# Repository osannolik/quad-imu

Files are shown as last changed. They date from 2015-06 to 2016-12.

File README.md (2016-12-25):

Quadcopter or general 6 DOF IMU
===========================

## Hardware

* ARM Cortex-M4, STM32F405, 168 MHz, FPU
* Accelerometer and gyro ICM20608
* 2.4 GHz Transceiver nRF24L01+
* USB Power Manager with Li-Ion charger LTC3553
* USB to serial UART interface FT232RQ 

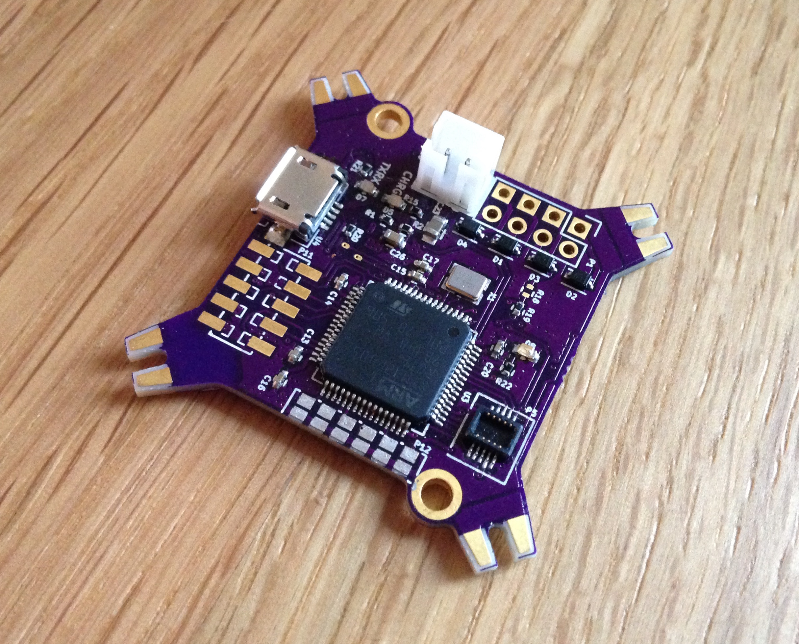
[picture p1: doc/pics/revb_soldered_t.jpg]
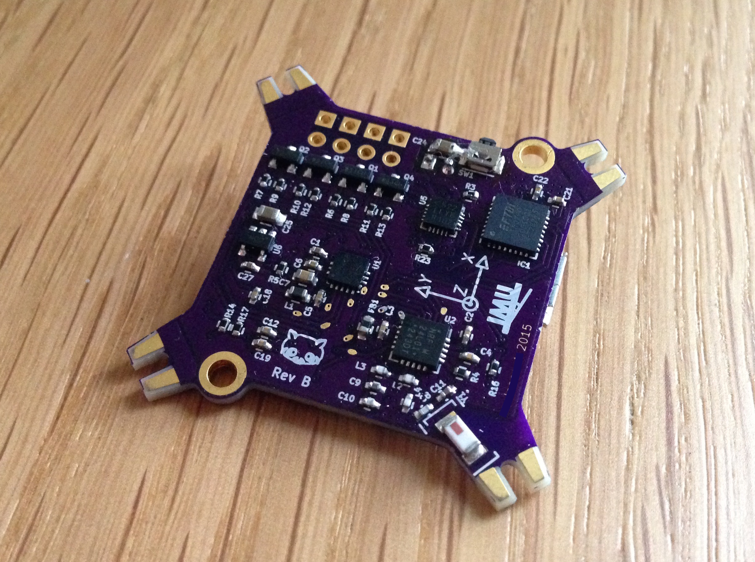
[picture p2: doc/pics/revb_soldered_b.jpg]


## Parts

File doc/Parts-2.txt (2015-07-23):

FT232R (dk 768-1008-1-ND)
USB B micro (dk 609-4052-1-ND)
Switch (dk SW1022CT-ND)

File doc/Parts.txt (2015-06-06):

//MPU-9250
ICM-20608 (dk 1428-1052-1-ND)
STM32F405RGT6 (dk 497-11767-ND)
nRF24L01P
LTC3553 (dk LTC3553EUD#PBF-ND)
//LTC4063 (dk LTC4063EDD#PBF-ND)
LED 0603 (dk 475-2512-1-ND)
//LP2992 LDO (dk LP2992AIM5-3.3/NOPBCT-ND)
TLV70033 LDO (dk 296-27937-1-ND)
Ferrite 0603 600ohm @ 100MHz (dk MH1608-601YCT-ND)
Inductor 0603 2.2uH (dk 445-3164-1-ND)
Chip antenna (dk 712-1005-1-ND)
BAT54WS SOD-323 (dk BAT54WS-TPCT-ND)
ST-Link v2 (dk 497-10484-ND)
ST-Link JTAG 20-10 pin converter (dk 1188-1016-ND)
Debug connector (dk H121938CT-ND) på kort
Debug connector (dk H124689CT-ND) på adapter
Crystal (dk SER3628CT-ND)
Caps 100nF 0402 (dk 1276-1001-1-ND)
Caps 470nF 0402 (dk 445-4996-1-ND)
Caps 33nF 0402 (dk 1276-1177-1-ND)
Caps 10nF 0402 (dk 1276-1051-1-ND)
Caps 1nF 0402 (dk 1276-1032-1-ND)
Caps 4.7uF 0603 (dk 1276-2087-1-ND)
Caps 2.2uF 0402 (dk 1276-1469-1-ND)
Caps 1uF 0402 (dk 1276-1444-1-ND)
Caps 10uF 0805 (dk 1276-2402-1-ND)
Caps 22uF 0805 (dk 1276-2412-1-ND)

Header female 2mm 2x5 (dk H10963-ND)
USB B micro (dk 609-4052-1-ND)
Resistors 0402 ...

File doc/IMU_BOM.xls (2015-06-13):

Reference | Quantity | Value | Footprint | Digikey | Buy qty
C1 | 1 | 470n | Capacitors_SMD:C_0402 | 445-4996-1-ND | 10
C10 | 1 | 4p7 | Capacitors_SMD:C_0402 |  | 0
C11 | 1 | 1p | Capacitors_SMD:C_0402 |  | 0
C12 C13 | 2 | 2u2 | Capacitors_SMD:C_0402 | 1276-1469-1-ND | 10
C17 C27 | 2 | 1u | Capacitors_SMD:C_0402 | 1276-1444-1-ND | 10
C2 | 1 | 33n | Capacitors_SMD:C_0402 | 1276-1177-1-ND | 10
C23 C25 | 2 | 10u | Capacitors_SMD:C_0805 | 1276-2402-1-ND | 10
C24 | 1 | 22u | Capacitors_SMD:C_0805 | 1276-2412-1-ND | 10
C15 C3 | 2 | 10n | Capacitors_SMD:C_0402 | 1276-1051-1-ND | 100
C4 | 1 | 1n | Capacitors_SMD:C_0402 | 1276-1032-1-ND | 100
C14 C16 C18 C19 C20 C21 C22 C5 C6 | 9 | 100n | Capacitors_SMD:C_0402 | 1276-1001-1-ND | 100
C26 C7 | 2 | 4u7 | Capacitors_SMD:C_0603 | 1276-2087-1-ND | 10
C8 | 1 | 1p5 | Capacitors_SMD:C_0402 |  | 0
C9 | 1 | 2n2 | Capacitors_SMD:C_0402 |  | 0
D1 D2 D3 D4 | 4 | BAT54WS | Diodes_SMD:SOD-323 | BAT54WS-TPCT-ND | 10
D6 | 1 | TXLED | LEDs:LED-0603 | 754-1121-1-ND | 10
D7 | 1 | RXLED | LEDs:LED-0603 |  | 0
D5 D8 | 2 | LED | LEDs:LED-0603 | 475-2512-1-ND | 10
FB1 | 1 | 600R@100MHz | Capacitors_SMD:C_0603 | MH1608-601YCT-ND | 10
IC1 | 1 | FT232RQ | Housings_DFN_QFN:QFN-32-1EP_5x5mm_Pitch0.5mm |  | 0
L1 | 1 | 2u2 | Capacitors_SMD:C_0603 | 445-3164-1-ND | 5
L2 | 1 | 8n2 | Capacitors_SMD:C_0402 |  | 0
L3 | 1 | 2n7 | Capacitors_SMD:C_0402 |  | 0
L4 | 1 | 3n9 | Capacitors_SMD:C_0402 |  | 0
P1 | 1 | M1P | Wire_Pads:SolderWirePad_single_0-8mmDrill
P10 | 1 | CONN_01X02 | w_conn_jst-ph:b2b-ph-kl |  | 0
P11 | 1 | CONN_02X05 | molexNoHole:molexNoHole-87832-10 | H10963-ND | 2
P12 | 1 | CONN_02X06 | Connect:GS_6x2
P2 | 1 | M1N | Wire_Pads:SolderWirePad_single_0-8mmDrill
P3 | 1 | M3P | Wire_Pads:SolderWirePad_single_0-8mmDrill
P4 | 1 | M3N | Wire_Pads:SolderWirePad_single_0-8mmDrill
P5 | 1 | JTAG_DB | DF23C-10DP-0.5V:DF23C-10DP-0.5V | H121938CT-ND | 4
P6 | 1 | M2P | Wire_Pads:SolderWirePad_single_0-8mmDrill
P7 | 1 | M2N | Wire_Pads:SolderWirePad_single_0-8mmDrill
P8 | 1 | M4P | Wire_Pads:SolderWirePad_single_0-8mmDrill
P9 | 1 | M4N | Wire_Pads:SolderWirePad_single_0-8mmDrill
Q1 Q2 Q3 Q4 | 4 | IRFML8244 | Housings_SOT-23_SOT-143_TSOT-6:SOT-23 |  | 0
R1 | 1 | 560k | Resistors_SMD:R_0402 | 541-560KLCT-ND | 10
R10 R11 R14 R16 R17 R6 R7 | 7 | 100 | Resistors_SMD:R_0402 | 541-100JCT-ND | 20
R12 R13 R5 R8 R9 | 5 | 10k | Resistors_SMD:R_0402 | 541-10KJCT-ND | 20
R18 R19 | 2 | 100k | Resistors_SMD:R_0402 | 541-100KJCT-ND | 10
R2 | 1 | 180k | Resistors_SMD:R_0402 | 541-180KLCT-ND | 10
R15 R20 R21 R22 | 4 | 2k2 | Resistors_SMD:R_0402 | 541-2.2KJCT-ND | 10
R3 | 1 | 3k6 | Resistors_SMD:R_0402 | 541-3.6KJCT-ND | 10
R4 | 1 | 22k | Resistors_SMD:R_0402 | 541-22KJCT-ND | 10
U1 | 1 | ICM20608 | LGA16:LGA16 | 1428-1052-1-ND | 1
U2 | 1 | NRF24L01 | Housings_DFN_QFN:QFN-20-1EP_4x4mm_Pitch0.5mm |  | 0
U3 | 1 | STM32F405 | Housings_QFP:LQFP-64_10x10mm_Pitch0.5mm | 497-11767-ND | 1
U4 | 1 | MICRO-B_USB | USB-B-Micro:USB-B-Micro | 609-4052-1-ND | 1
U5 | 1 | LTC3553 | Housings_DFN_QFN:UQFN-20-1EP_3x3mm_Pitch0.4mm | LTC3553EUD#PBF-ND | 1
U6 | 1 | TLV70033 | Housings_SOT-23_SOT-143_TSOT-6:SOT-23-5 | 296-27937-1-ND | 1
X1 | 1 | 16MHz | Crystals_Oscillators_SMD:crystal_FA238-TSX3225 | SER3628CT-ND | 1
Y1 | 1 | CHIP_ANTENNA | ANTENNA-JOHANSON-2.45GHZ:ANTENNA-JOHANSON-2.45GHZ | 712-1005-1-ND | 1
 |  |  | Debug connector receptacle | H124689CT-ND | 4
 |  |  | ST-Link V2 | 497-10484-ND | 1
http://www.digikey.se/short/718pn9

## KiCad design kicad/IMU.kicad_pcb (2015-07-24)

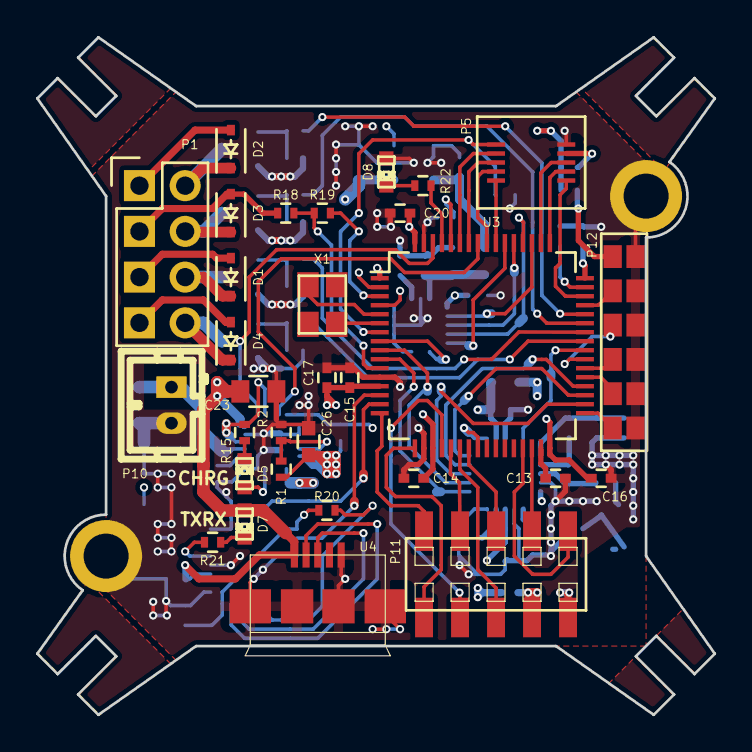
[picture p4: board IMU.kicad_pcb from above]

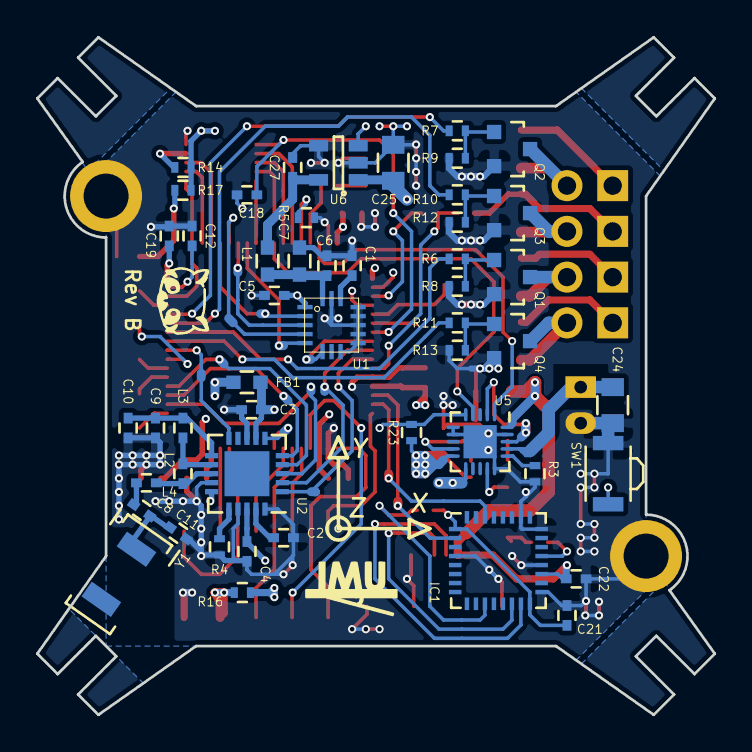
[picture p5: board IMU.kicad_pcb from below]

Board: 4 copper layers, 37.6 x 37.6 mm, 83 parts (50 on the bottom side), 88 nets.

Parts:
C1: 470n; C_0402
C2: 33n; C_0402
C3, C15: 10n; C_0402
C4: 1n; C_0402
C5, C6, C14, C16, C18, C19, C20, C21, C22: 100n; C_0402
C7, C26: 4u7; C_0603
C8: 1p5; C_0402
C9: 2n2; C_0402
C10: 4p7; C_0402
C11: 1p; C_0402
C12, C13: 2u2; C_0402
C17, C27: 1u; C_0402
C23, C24, C25: 10u; C_0805
D1, D2, D3, D4: BAT54WS; SOD-323
D5, D8: LED; LED-0603
D7: TXRXLED; LED-0603
FB1: 600R@100MHz; C_0603
IC1: FT232RQ; QFN-32-1EP_5x5mm_Pitch0.5mm
L1: 2u2; C_0603
L2: 8n2; C_0402
L3: 2n7; C_0402
L4: 3n9; C_0402
MH1, MH2: Mounting; MountingHole_2-5mm
P1: CONN_02X04; Pin_Header_Straight_2x04
P5: JTAG_DB; DF23C-10DP-0.5V
P10: CONN_01X02; b2b-ph-kl
P11: CONN_02X05; molexNoHole-87832-10
P12: CONN_02X06; GS_6x2
Q1, Q2, Q3, Q4: IRFML8244; SOT-23
R1: 560k; R_0402
R2: 180k; R_0402
R3: 3k6; R_0402
R4: 22k; R_0402
R5, R8, R9, R12, R13, R20: 10k; R_0402
R6, R7, R10, R11, R14, R16, R17: 100; R_0402
R15, R21, R22: 2k2; R_0402
R18, R19, R23: 100k; R_0402
SW1: SW_PUSH; B3U_3000P
U1: ICM20608; LGA16
U2: NRF24L01; QFN-20-1EP_4x4mm_Pitch0.5mm
U3: STM32F405; LQFP-64_10x10mm_Pitch0.5mm
U4: MICRO-B_USB; USB-B-Micro
U5: LTC3553; UQFN-20-1EP_3x3mm_Pitch0.4mm
U6: TLV70033; SOT-23-5
X1: 16MHz; crystal_FA238-TSX3225
Y1: CHIP_ANTENNA; ANTENNA-JOHANSON-2.45GHZ

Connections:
+5V: C22.1, C23.1, D7.2, IC1.19, U4.1, U5.20
+BATT: C24.1, D1.2, D2.2, D3.2, D4.2, P1.1, P1.3, P1.5, P1.7, P10.1, R18.1, U5.17
/Mems and Radio/MEMS_CS: U1.5, U3.54
/Mems and Radio/MEMS_INT: U1.6, U3.8
/Mems and Radio/MEMS_MISO: U1.4, U3.52
/Mems and Radio/MEMS_MOSI: U1.3, U3.53
/Mems and Radio/MEMS_SCLK: U1.2, U3.51
/Mems and Radio/NRF24_CE: U2.1, U3.10
/Mems and Radio/NRF24_CSN: U2.2, U3.9
/Mems and Radio/NRF24_IRQ: U2.6, U3.24
/Mems and Radio/NRF24_MISO: U2.5, U3.35
/Mems and Radio/NRF24_MOSI: U2.4, U3.36
/Mems and Radio/NRF24_OSC: U2.10, U3.40
/Mems and Radio/NRF24_SCK: U2.3, U3.34
/Microcontroller/CON_CLK: P11.4, U3.21
/Microcontroller/CON_DAC: P11.3, U3.20
/Microcontroller/CON_MISO: P11.5, U3.22
/Microcontroller/CON_MOSI: P11.6, U3.23
/Microcontroller/CON_RX: P11.1, U3.17
/Microcontroller/CON_SCL: P11.10, U3.29
/Microcontroller/CON_SDA: P11.8, U3.30
/Microcontroller/CON_TX: P11.2, U3.16
/Microcontroller/DB_RX: P5.3, U3.59
/Microcontroller/DB_TX: P5.5, U3.58
/Microcontroller/HPWR: U3.62, U5.1
/Microcontroller/LDO_ON: R23.2, U3.2, U5.5
/Microcontroller/M1: R6.2, U3.42
/Microcontroller/M1N: D1.1, P1.6, Q1.3
/Microcontroller/M2: R10.2, U3.43
/Microcontroller/M2N: D3.1, P1.4, Q3.3
/Microcontroller/M3: R7.2, U3.44
/Microcontroller/M3N: D2.1, P1.2, Q2.3
/Microcontroller/M4: R11.2, U3.41
/Microcontroller/M4N: D4.1, P1.8, Q4.3
/Microcontroller/NJTRST: P5.7, U3.56
/Microcontroller/NRST: C18.1, P5.1, U3.7
/Microcontroller/PAD1: P12.3, U3.45
/Microcontroller/PAD2: P12.5, U3.39
/Microcontroller/PAD3: P12.7, U3.38
/Microcontroller/PAD4: P12.9, U3.37
/Microcontroller/PAD5: P12.11, U3.33
/Microcontroller/PWREN#: IC1.11, R20.2, U3.4
/Microcontroller/TCK/SWDCLK: P5.8, U3.49
/Microcontroller/TDI: P5.6, U3.50
/Microcontroller/TDO/SWO: P5.9, U3.55
/Microcontroller/TMS/SWDIO: P5.10, U3.46
/Microcontroller/VBAT: R18.2, R19.1, U3.11
/Microcontroller/VBAT0: R19.2, U3.3
/Microcontroller/~ON: SW1.2, U3.57, U5.4
/Power/FTDI_RXD: IC1.2, U3.14
/Power/FTDI_TXD: IC1.30, U3.15
/Power/VccIO: C21.1, IC1.1, IC1.16, R20.1
/Power/Vout: C25.1, R15.1, U5.2, U5.11, U5.18, U6.1, U6.3
GND: C1.2, C2.2, C3.2, C4.2, C5.2, C6.2, C7.2, C9.2, C10.2, C11.1, C12.2, C13.2, C14.2, C15.2, C16.2, C17.2, C18.2, C19.2, C20.2, C21.2, C22.2, C23.2, C24.2, C25.2, C26.2, C27.2, D8.2, IC1.4, IC1.17, IC1.20, IC1.24, IC1.26, MH1.1, MH2.1, P5.2, P10.2, P11.9, P12.2, P12.4, P12.6, P12.8, P12.10, P12.12, Q1.2, Q2.2, Q3.2, Q4.2, R2.2, R3.2, R4.2, R5.1, R8.2, R9.2, R12.2, R13.2, SW1.1, U1.8, U1.9, U1.10, U1.11, U1.12, U1.13, U1.15, U2.8, U2.14, U2.17, U2.20, U3.12, U3.18, U3.63, U4.5, U5.6, U5.7, U5.15, U5.19, U5.21, U6.2, U6.4
unnamed: C1.1, U1.14
unnamed: C2.1, U2.19
unnamed: C3.1, C4.1, FB1.1, U2.7, U2.15, U2.18
unnamed: C6.1, C7.1, L1.2, U1.16
unnamed: C8.2, L4.2
unnamed: C9.1, C10.1, L3.2, U2.11
unnamed: C8.1, C11.2, Y1.1
unnamed: C12.1, U3.47
unnamed: C13.1, U3.31
unnamed: D5.1, R15.2
unnamed: D5.2, U5.14
unnamed: D7.1, R21.1
unnamed: D8.1, R22.2
unnamed: IC1.14, U4.3
unnamed: IC1.15, U4.2
unnamed: IC1.21, R21.2
unnamed: L2.1, L3.1, U2.12
unnamed: L2.2, L4.1, U2.13
unnamed: P5.4, R14.1
unnamed: P11.7, R16.2
unnamed: P12.1, R17.2
unnamed: Q1.1, R6.1, R8.1
unnamed: Q2.1, R7.1, R9.1
unnamed: Q3.1, R10.1, R12.1
unnamed: Q4.1, R11.1, R13.1
unnamed: R1.2, R2.1, U5.9
unnamed: R3.1, U5.16
unnamed: R4.1, U2.16
unnamed: R5.2, U3.60
unnamed: R22.1, U3.61
unnamed: U3.5, X1.2
unnamed: U3.6, X1.1
VAA: C27.1, L1.1, U6.5
VDD: C5.1, C14.1, C15.1, C16.1, C17.1, C19.1, C20.1, C26.1, FB1.2, R1.1, R14.2, R16.1, R17.1, R23.1, U1.1, U3.1, U3.13, U3.19, U3.32, U3.48, U3.64, U5.10

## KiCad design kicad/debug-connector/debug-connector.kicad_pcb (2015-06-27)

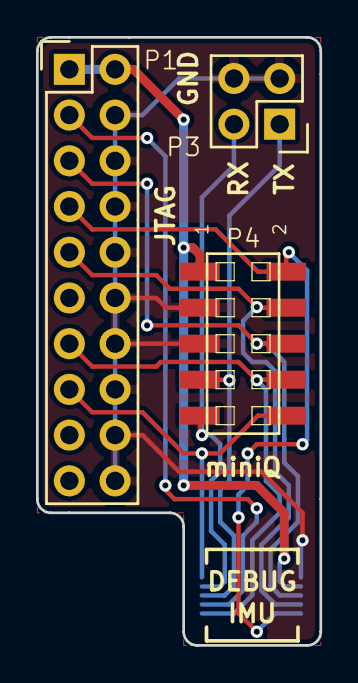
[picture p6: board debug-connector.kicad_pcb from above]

Board: 2 copper layers, 15.7 x 33.8 mm, 4 parts (1 on the bottom side), 10 nets.

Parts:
P1: CONN_02X10; Pin_Header_Straight_2x10
P2: CONN_02X05; DF23C-10DS-0.5V
P3: CONN_01X04; Pin_Header_Straight_2x02
P4: CONN_02X05; molexNoHole-87832-10

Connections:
/NRST: P1.15, P2.9, P4.10
/TCK_SWCLK: P1.9, P2.4, P4.4
/TDI: P1.5, P2.6, P4.6
/TDO_SWO: P1.13, P2.1, P4.8
/TMS_SWDIO: P1.7, P2.2, P4.2
/TRST: P1.3, P2.3
/UART_RX: P2.7, P3.2, P4.9
/UART_TX: P2.5, P3.1, P4.7
/VAPP: P1.1, P1.2, P2.8, P4.1
GND: P1.4, P1.6, P1.8, P1.10, P1.12, P1.14, P1.16, P1.18, P1.20, P2.10, P3.3, P3.4, P4.3, P4.5

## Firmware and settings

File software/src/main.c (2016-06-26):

#include "main.h"

static void SystemClock_Config(void);
static void Error_Handler(void);

int main(void)
{
  HAL_Init();
  /* Configure the system clock to 168 MHz */
  SystemClock_Config();


  debug_init();
  pwr_init();

  //app_kladd();

  radio_init();
  uart_init();
  com_init();

  calmeas_init();

  quadsys_init();



  //pwr_startup();

  while (1) {
    //orient_update();

    HAL_Delay(1);

    orient_param_update(100);

    calmeas_handler();

    com_handler();
  }

  //imuLgr_send();

  while (1) {
    if (pwr_getPwrEnSts()) {
      HAL_Delay(200);
      DBG_LED_RESET;
      HAL_Delay(200);
      DBG_LED_SET;
    } else {
      HAL_Delay(50);
      DBG_LED_RESET;
      HAL_Delay(50);
      DBG_LED_SET;
    }
  }
}

/**
  * @brief  System Clock Configuration
  *         The system Clock is configured as follow : 
  *            System Clock source            = PLL (HSE)
  *            SYSCLK(Hz)                     = 168000000
  *            HCLK(Hz)                       = 168000000
  *            AHB Prescaler                  = 1
  *            APB1 Prescaler                 = 4
  *            APB2 Prescaler                 = 2
  *            HSE Frequency(Hz)              = 8000000
  *            PLL_M                          = 8 => 16
  *            PLL_N                          = 336
  *            PLL_P                          = 2
  *            PLL_Q                          = 7
  *            VDD(V)                         = 3.3
  *            Main regulator output voltage  = Scale1 mode
  *            Flash Latency(WS)              = 5
  * @param  None
  * @retval None
  */
static void SystemClock_Config(void)
{
  RCC_ClkInitTypeDef RCC_ClkInitStruct;
  RCC_OscInitTypeDef RCC_OscInitStruct;
  
  /* Enable Power Control clock */
  __HAL_RCC_PWR_CLK_ENABLE();
  
  /* The voltage scaling allows optimizing the power consumption when the device is 
     clocked below the maximum system frequency, to update the voltage scaling value 
     regarding system frequency refer to product datasheet.  */
  __HAL_PWR_VOLTAGESCALING_CONFIG(PWR_REGULATOR_VOLTAGE_SCALE1);

  /* Enable HSE Oscillator and activate PLL with HSE as source */
  RCC_OscInitStruct.OscillatorType = RCC_OSCILLATORTYPE_HSE;
  RCC_OscInitStruct.HSEState = RCC_HSE_ON;
  RCC_OscInitStruct.PLL.PLLState = RCC_PLL_ON;
  RCC_OscInitStruct.PLL.PLLSource = RCC_PLLSOURCE_HSE;
  RCC_OscInitStruct.PLL.PLLM = 16;
  RCC_OscInitStruct.PLL.PLLN = 336;
  RCC_OscInitStruct.PLL.PLLP = RCC_PLLP_DIV2;
  RCC_OscInitStruct.PLL.PLLQ = 7;
  if(HAL_RCC_OscConfig(&RCC_OscInitStruct) != HAL_OK)
  {
    /* Initialization Error */
    Error_Handler();
  }
  
  /* Select PLL as system clock source and configure the HCLK, PCLK1 and PCLK2 
     clocks dividers */
  RCC_ClkInitStruct.ClockType = (RCC_CLOCKTYPE_SYSCLK | RCC_CLOCKTYPE_HCLK | RCC_CLOCKTYPE_PCLK1 | RCC_CLOCKTYPE_PCLK2);
  RCC_ClkInitStruct.SYSCLKSource = RCC_SYSCLKSOURCE_PLLCLK;
  RCC_ClkInitStruct.AHBCLKDivider = RCC_SYSCLK_DIV1;
  RCC_ClkInitStruct.APB1CLKDivider = RCC_HCLK_DIV4;  
  RCC_ClkInitStruct.APB2CLKDivider = RCC_HCLK_DIV2;  
  if(HAL_RCC_ClockConfig(&RCC_ClkInitStruct, FLASH_LATENCY_5) != HAL_OK)
  {
    /* Initialization Error */
    Error_Handler();
  }

  /* STM32F405x/407x/415x/417x Revision Z devices: prefetch is supported  */
  if (HAL_GetREVID() == 0x1001)
  {
    /* Enable the Flash prefetch */
    __HAL_FLASH_PREFETCH_BUFFER_ENABLE();
  }
}

static void Error_Handler(void)
{
  /* User may add here some code to deal with this error */
  while(1)
  {
  }
}

#ifdef  USE_FULL_ASSERT

/**
  * @brief  Reports the name of the source file and the source line number
  *         where the assert_param error has occurred.
  * @param  file: pointer to the source file name
  * @param  line: assert_param error line source number
  * @retval None
  */
void assert_failed(uint8_t* file, uint32_t line)
{ 
  /* User can add his own implementation to report the file name and line number,
     ex: printf("Wrong parameters value: file %s on line %d\r\n", file, line) */

  /* Infinite loop */
  while (1)
  {
  }
}
#endif

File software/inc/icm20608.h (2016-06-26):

/*
 * icm20608.h
 *
 *  Created on: 24 jun 2016
 *      Author: osannolik
 */

#ifndef ICM20608_H_
#define ICM20608_H_

#include "stm32f4xx_hal.h"

#define ICM20608_SPI_INSTANCE  SPI3

#define ICM20608_MOSI_PIN      GPIO_PIN_12
#define ICM20608_MOSI_PORT     GPIOC
#define ICM20608_MISO_PIN      GPIO_PIN_11
#define ICM20608_MISO_PORT     GPIOC
#define ICM20608_SCK_PIN       GPIO_PIN_10
#define ICM20608_SCK_PORT      GPIOC
#define ICM20608_CS_PIN        GPIO_PIN_2
#define ICM20608_CS_PORT       GPIOD
#define ICM20608_IRQ_PIN       GPIO_PIN_0
#define ICM20608_IRQ_PORT      GPIOC

#define ICM20608_SPIWRRD_TIOUT (1000)

#define ICM20608_DUMMYDATA (0x00)

// Operations
#define ICM20608_RD_REG (0x80)
#define ICM20608_WR_REG (0x00)

// Registers
#define ICM20608_RM_SELF_TEST_X_GYRO  (0x00)
#define ICM20608_RM_SELF_TEST_Y_GYRO  (0x01)
#define ICM20608_RM_SELF_TEST_Z_GYRO  (0x02)
#define ICM20608_RM_SELF_TEST_X_ACCEL (0x0D)
#define ICM20608_RM_SELF_TEST_Y_ACCEL (0x0E)
#define ICM20608_RM_SELF_TEST_Z_ACCEL (0x0F)
#define ICM20608_RM_XG_OFFS_USRH      (0x13)
#define ICM20608_RM_XG_OFFS_USRL      (0x14)
#define ICM20608_RM_YG_OFFS_USRH      (0x15)
#define ICM20608_RM_YG_OFFS_USRL      (0x16)
#define ICM20608_RM_ZG_OFFS_USRH      (0x17)
#define ICM20608_RM_ZG_OFFS_USRL      (0x18)
#define ICM20608_RM_SMPLRT_DIV        (0x19)
#define ICM20608_RM_CONFIG            (0x1A)
#define ICM20608_RM_GYRO_CONFIG       (0x1B)
#define ICM20608_RM_ACCEL_CONFIG      (0x1C)
#define ICM20608_RM_ACCEL_CONFIG_2    (0x1D)
#define ICM20608_RM_LP_MODE_CFG       (0x1E)
#define ICM20608_RM_ACCEL_WOM_THR     (0x1F)
#define ICM20608_RM_FIFO_EN           (0x23)
#define ICM20608_RM_FSYNC_INT         (0x36)
#define ICM20608_RM_INT_PIN_CFG       (0x37)
#define ICM20608_RM_INT_ENABLE        (0x38)
#define ICM20608_RM_INT_STATUS        (0x3A)
#define ICM20608_RM_ACCEL_XOUT_H      (0x3B)
#define ICM20608_RM_ACCEL_XOUT_L      (0x3C)
#define ICM20608_RM_ACCEL_YOUT_H      (0x3D)
#define ICM20608_RM_ACCEL_YOUT_L      (0x3E)
#define ICM20608_RM_ACCEL_ZOUT_H      (0x3F)
#define ICM20608_RM_ACCEL_ZOUT_L      (0x40)
#define ICM20608_RM_TEMP_OUT_H        (0x41)
#define ICM20608_RM_TEMP_OUT_L        (0x42)
#define ICM20608_RM_GYRO_XOUT_H       (0x43)
#define ICM20608_RM_GYRO_XOUT_L       (0x44)
#define ICM20608_RM_GYRO_YOUT_H       (0x45)
#define ICM20608_RM_GYRO_YOUT_L       (0x46)
#define ICM20608_RM_GYRO_ZOUT_H       (0x47)
#define ICM20608_RM_GYRO_ZOUT_L       (0x48)
#define ICM20608_RM_SIGNAL_PATH_RESET (0x68)
#define ICM20608_RM_ACCEL_INTEL_CTRL  (0x69)
#define ICM20608_RM_USER_CTRL         (0x6A)
#define ICM20608_RM_PWR_MGMT_1        (0x6B)
#define ICM20608_RM_PWR_MGMT_2        (0x6C)
#define ICM20608_RM_FIFO_COUNTH       (0x72)
#define ICM20608_RM_FIFO_COUNTL       (0x73)
#define ICM20608_RM_FIFO_R_W          (0x74)
#define ICM20608_RM_WHO_AM_I          (0x75)
#define ICM20608_RM_XA_OFFSET_H       (0x77)
#define ICM20608_RM_XA_OFFSET_L       (0x78)
#define ICM20608_RM_YA_OFFSET_H       (0x7A)
#define ICM20608_RM_YA_OFFSET_L       (0x7B)
#define ICM20608_RM_ZA_OFFSET_H       (0x7D)
#define ICM20608_RM_ZA_OFFSET_L       (0x7E)

// Register bit definitions
#define _BIT(x) (0x01<<(x))

#define ICM20608_CONFIG_FIFO_MODE (_BIT(6))
#define ICM20608_CONFIG_EXT_SYNC  (_BIT(5) | _BIT(4) | _BIT(3))
#define ICM20608_CONFIG_DLPF_CFG  (_BIT(2) | _BIT(1) | _BIT(0))

#define ICM20608_CONFIG_EXT_SYNC_SET(X) (ICM20608_CONFIG_EXT_SYNC & (X<<3))
#define ICM20608_CONFIG_DLPF_CFG_SET(X) (ICM20608_CONFIG_DLPF_CFG & X)

#define ICM20608_GYRO_CONFIG_XG_ST     (_BIT(7))
#define ICM20608_GYRO_CONFIG_YG_ST     (_BIT(6))
#define ICM20608_GYRO_CONFIG_ZG_ST     (_BIT(5))
#define ICM20608_GYRO_CONFIG_FS_SEL    (_BIT(4) | _BIT(3))
#define ICM20608_GYRO_CONFIG_FCHOICE_B (_BIT(1) | _BIT(0))

#define ICM20608_GYRO_CONFIG_FCHOICE_B_SET(X) (ICM20608_GYRO_CONFIG_FCHOICE_B & X)
#define ICM20608_GYRO_CONFIG_FS_SEL_SET(X)    (ICM20608_GYRO_CONFIG_FS_SEL & ((X) << 3))
#define ICM20608_GYRO_CONFIG_FS_SEL_250DPS    ICM20608_GYRO_CONFIG_FS_SEL_SET(0)
#define ICM20608_GYRO_CONFIG_FS_SEL_500DPS    ICM20608_GYRO_CONFIG_FS_SEL_SET(1)
#define ICM20608_GYRO_CONFIG_FS_SEL_1000DPS   ICM20608_GYRO_CONFIG_FS_SEL_SET(2)
#define ICM20608_GYRO_CONFIG_FS_SEL_2000DPS   ICM20608_GYRO_CONFIG_FS_SEL_SET(3)

#define ICM20608_GYRO_LSB_PER_DEGPERSEC(FS_SEL) ((float)(1<<15))/((float)(250<<FS_SEL))

#define ICM20608_GYRO_DEGPERSEC_PER_LSB(FS_SEL) (0.007633587786 * ((float) (1<<FS_SEL)))

#define ICM20608_ACCEL_CONFIG_XA_ST  (_BIT(7))
#define ICM20608_ACCEL_CONFIG_YA_ST  (_BIT(6))
#define ICM20608_ACCEL_CONFIG_ZA_ST  (_BIT(5))
#define ICM20608_ACCEL_CONFIG_FS_SEL (_BIT(4) | _BIT(3))

#define ICM20608_ACCEL_CONFIG_FS_SEL_SET(X) (ICM20608_ACCEL_CONFIG_FS_SEL & ((X) << 3))
#define ICM20608_ACCEL_CONFIG_FS_SEL_2G     ICM20608_ACCEL_CONFIG_FS_SEL_SET(0)
#define ICM20608_ACCEL_CONFIG_FS_SEL_4G     ICM20608_ACCEL_CONFIG_FS_SEL_SET(1)
#define ICM20608_ACCEL_CONFIG_FS_SEL_8G     ICM20608_ACCEL_CONFIG_FS_SEL_SET(2)
#define ICM20608_ACCEL_CONFIG_FS_SEL_16G    ICM20608_ACCEL_CONFIG_FS_SEL_SET(3)

#define ICM20608_ACCEL_LSB_PER_G(FS_SEL) (1<<15)/(2<<FS_SEL)

#define ICM20608_ACCEL_CONFIG_2_DEC2_CFG   (_BIT(5) | _BIT(4))
#define ICM20608_ACCEL_CONFIG_2_FCHOICE_B  (_BIT(3))
#define ICM20608_ACCEL_CONFIG_2_A_DLPF_CFG (_BIT(2) | _BIT(1) | _BIT(0))

#define ICM20608_ACCEL_CONFIG_2_DEC2_CFG_SET(X)   (ICM20608_ACCEL_CONFIG_2_DEC2_CFG & ((X) << 4))
#define ICM20608_ACCEL_CONFIG_2_FCHOICE_B_SET(X)  (ICM20608_ACCEL_CONFIG_2_FCHOICE_B & ((X) << 3))
#define ICM20608_ACCEL_CONFIG_2_A_DLPF_CFG_SET(X) (ICM20608_ACCEL_CONFIG_2_A_DLPF_CFG & X)

#define ICM20608_ACCEL_CONFIG_2_DEC2_CFG_AVG4  (0x00)
#define ICM20608_ACCEL_CONFIG_2_DEC2_CFG_AVG8  (_BIT(4))
#define ICM20608_ACCEL_CONFIG_2_DEC2_CFG_AVG16 (_BIT(5))
#define ICM20608_ACCEL_CONFIG_2_DEC2_CFG_AVG32 (_BIT(5) | _BIT(4))

#define ICM20608_LP_MODE_CFG_GYRO_CYCLE   (_BIT(7))
#define ICM20608_LP_MODE_CFG_G_AVGCFG     (_BIT(6) | _BIT(5) | _BIT(4))
#define ICM20608_LP_MODE_CFG_LPOSC_CLKSEL (_BIT(3) | _BIT(2) | _BIT(1) | _BIT(0))

#define ICM20608_LP_MODE_CFG_G_AVGCFG_SET(X) (ICM20608_LP_MODE_CFG_G_AVGCFG & ((X) << 4))
#define ICM20608_LP_MODE_CFG_LPOSC_CLKSEL_SET(X) (ICM20608_LP_MODE_CFG_LPOSC_CLKSEL & X)

#define ICM20608_LP_MODE_CFG_LPOSC_CLKSEL_0HZ24  (0)
#define ICM20608_LP_MODE_CFG_LPOSC_CLKSEL_0HZ49  (1)
#define ICM20608_LP_MODE_CFG_LPOSC_CLKSEL_0HZ98  (2)
#define ICM20608_LP_MODE_CFG_LPOSC_CLKSEL_1HZ95  (3)
#define ICM20608_LP_MODE_CFG_LPOSC_CLKSEL_3HZ91  (4)
#define ICM20608_LP_MODE_CFG_LPOSC_CLKSEL_7HZ81  (5)
#define ICM20608_LP_MODE_CFG_LPOSC_CLKSEL_15HZ63 (6)
#define ICM20608_LP_MODE_CFG_LPOSC_CLKSEL_31HZ25 (7)
#define ICM20608_LP_MODE_CFG_LPOSC_CLKSEL_62HZ50 (8)
#define ICM20608_LP_MODE_CFG_LPOSC_CLKSEL_125HZ  (9)
#define ICM20608_LP_MODE_CFG_LPOSC_CLKSEL_250HZ  (10)
#define ICM20608_LP_MODE_CFG_LPOSC_CLKSEL_500HZ  (11)
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

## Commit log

2015-05-30 First commit. Files migrated from Dropbox.
    [IMU.kicad_pcb, IMU.sch, mcu.sch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]
2015-05-31 Added edge pads and some more vias.
    [IMU.kicad_pcb, IMU.sch, mcu.sch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]
2015-06-01 Added status LEDs to FTDI IC and bat voltage to mcu ADC.
    [IMU.kicad_pcb, IMU.sch, mcu.sch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]
2015-06-02 Changed LP2992 to TLV700 with better PSRR.
    [IMU.kicad_pcb, IMU.sch, mcu.sch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]
2015-06-02 Placed ref text on pcb.
    [IMU.kicad_pcb]
2015-06-03 Moved USB and external edge connector and re-routed FTDI IC.
    [IMU.kicad_pcb, mcu.sch]
2015-06-06 Replaced USB connector footprint.
    [IMU.kicad_pcb, power.sch]
2015-06-06 Added debug LED to mcu pin.
    [IMU.kicad_pcb, mcu.sch, power.sch]
2015-06-06 Cleared corner areas to allow for arm attachments.
    [IMU.kicad_pcb]
2015-06-07 Added shoulders for arms at corners.
    [IMU.kicad_pcb]
2015-06-08 Add solder pads to arm-mountings.
    [IMU.kicad_pcb]
2015-06-09 Change clearance of power planes and add logos. Generate BOM.
    [IMU.kicad_pcb, IMU_BOM.xls]
2015-06-10 Connect CS of MEMS to mcu.
    [IMU.kicad_pcb, IMU.sch, mcu.sch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]
2015-06-11 Update BOM with pn.
    [IMU_BOM.xls]
2015-06-13 Add mounting holes and XYZ-silkscreen.
    [IMU.kicad_pcb, mcu.sch, power.sch]
2015-06-13 Move panda logo.
    [IMU.kicad_pcb]
2015-06-13 Digikey cart and oshpark gerbers added.
    [IMU_BOM.xls]
2015-06-13 Reorganized parts and BOM.
    [IMU_BOM.xls]
2015-06-21 Created debug connector receptacle footprint.
2015-06-21 Changed R,C and D's in sch from old standard lib to new lib. Move GND-via under debug connector.
    [IMU.kicad_pcb, IMU.sch, mcu.sch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]
2015-06-21 Work commit: Add debug connector project.
    [debug-connector.sch]
2015-06-23 First routing of debug connector pcb.
    [debug-connector.kicad_pcb, debug-connector.sch]
2015-06-24 Add outline and ground planes
    [debug-connector.kicad_pcb]
2015-06-25 Move debug connector to right and add text and logos on silkscreen.
    [debug-connector.kicad_pcb]
2015-06-27 Debug connector remade to better fit on IMU board.
    [debug-connector.kicad_pcb, debug-connector.sch]
2015-06-27 Add Debug connector Rev A gerbers.
2015-07-23 Corrected ON-circuitry of LTC3553, and other minor board changes.
    [IMU.kicad_pcb, IMU.sch, mcu.sch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]
2015-07-24 Connected mcu pin to LDO_ON.
    [IMU.kicad_pcb, IMU.sch, mcu.sch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]
2015-07-24 Gerbers generated for Rev B
    [IMU.kicad_pcb]
2015-07-24 First version of quad-arms
    [quad-arms.kicad_pcb]
